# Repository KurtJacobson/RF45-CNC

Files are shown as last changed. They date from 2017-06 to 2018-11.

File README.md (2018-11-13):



# RF45-CNC
Documentation, CAD models and LinuxCNC configs for ENCO RF45 CNC conversion

Google Photos Album: https://goo.gl/photos/A5knVXhwu5FXMWHDA  
CNCzone Build Thread: http://www.cnczone.com/forums/rf-45-clone-mill/326994-cnc-cad-engineering.html  



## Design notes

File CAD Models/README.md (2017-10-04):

# CAD Models

All CAD models and drawings were made using SolidWorks 16-17.  

Currently CAD achives are available in these formats:

  * SolidWorks 16-17
  * Fusion 360
  * IGS
  * STEP

I may be able to provide other CAD formats upon request. [Open an Issue][1]
and I will see what I can do for you.

**Note** You should Download this entire folder so the part relations stay intact.

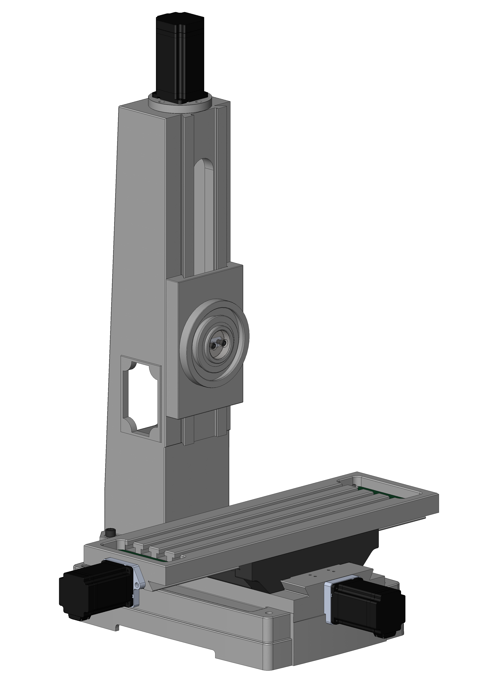
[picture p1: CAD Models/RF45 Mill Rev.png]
RF45 CAD Model Assy


[1]: https://github.com/KurtJacobson/RF45-CNC/issues/new

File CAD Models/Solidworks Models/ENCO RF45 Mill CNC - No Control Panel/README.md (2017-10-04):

# SolidWorks Models

These are SolidWorks 16-17 format solid models of the complete CNC conversion. 
I may be able to provide other CAD formats upon request, just [open an Issue][1]
and I will see what I can do for you.

**Note** You should Download this entire folder so the part relations stay intact. 

[1]: https://github.com/KurtJacobson/RF45-CNC/issues/new

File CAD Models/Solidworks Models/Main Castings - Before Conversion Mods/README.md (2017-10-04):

The CAD files in this folder are very accurate models of the original castings
before any modifications for CNC conversion. Very accurate means that critical
dimensions such as ways and hole locations are within about .005 of what they
measured on my machine, noncritical dimensions such as casting wall thicknesses
should be within about .05. You machine will likely very significantly from mine,
use with discretion.

File format is Solidworks 2016-17.  I might be able to provide other file formats 
on request.

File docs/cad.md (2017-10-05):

# CAD Models

All CAD models and drawings were made using SolidWorks 16-17. 

## CAD Archives

These are archives that I have made for various people over time. They may not
be up to date. If you can use SolidWorks files then you should download from 
the [SolidWorks Modles][2] directory.

CAD archives are available in these formats:

  * SolidWorks 16-17
  * Fusion 360
  * STEP
  * IGS

These files are located in the [`CAD Models/CAD Archives`][1] directory.

I may be able to provide other CAD formats upon request. [Open an Issue][i]
and I will see what I can do for you.

## SolidWorks Models

This is my working directory and has the most up to date models. There are two
subdirectories, one contains the models of the main castings pre-conversion, and
before any modifications. The other contains the models of the converted machine.

These files are located in the [`CAD Models/SolidWorks Models`][2] directory and
are all in SolidWorks 16-17 format.

[1]: https://github.com/KurtJacobson/RF45-CNC/tree/master/CAD%20Models/CAD%20Archives
[2]: https://github.com/KurtJacobson/RF45-CNC/tree/master/CAD%20Models/Solidworks%20Models

[i]: https://github.com/KurtJacobson/RF45-CNC/issues/new

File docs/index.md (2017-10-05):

# RF45 CNC Conversion

!!! note ""
    I will be moving all the CAD and other files from my [Google drive][1] site to here.

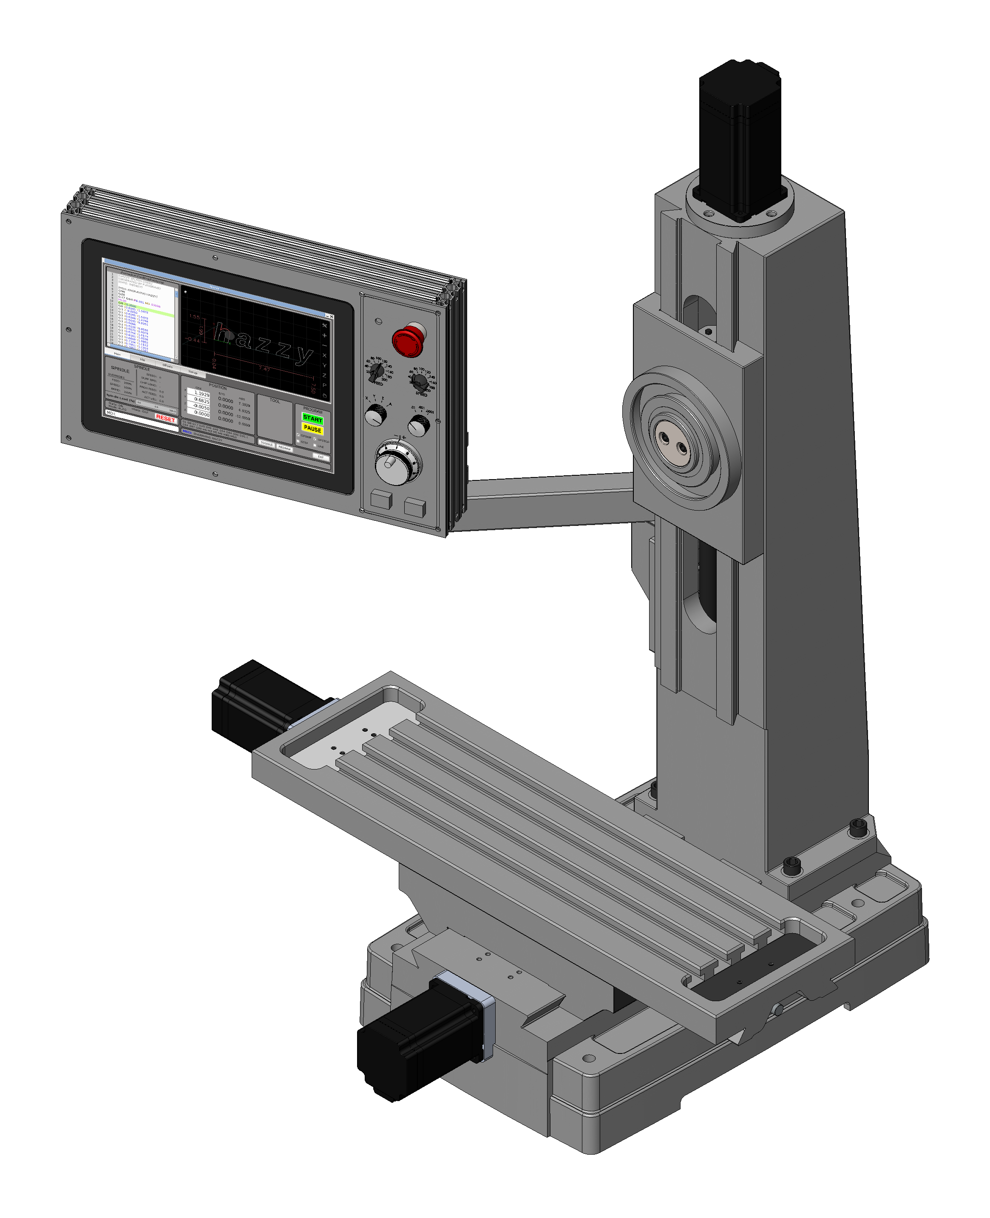
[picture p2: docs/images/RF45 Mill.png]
ENCO RF45 Clone Mill


[1]: https://drive.google.com/open?id=0B0f9qd4rM52xaklJd1I3blZVd1k

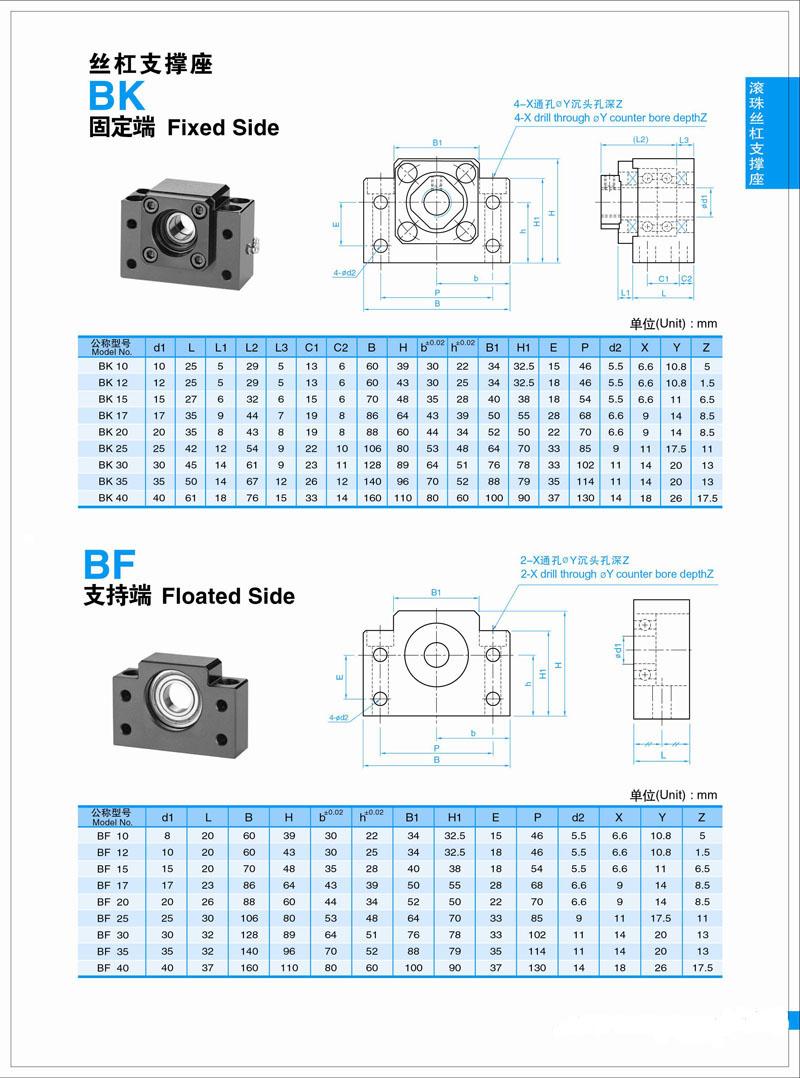
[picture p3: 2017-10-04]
CAD Models/Solidworks Models/ENCO RF45 Mill CNC - No Control Panel/X-axis/BK15/BK BF.jpg

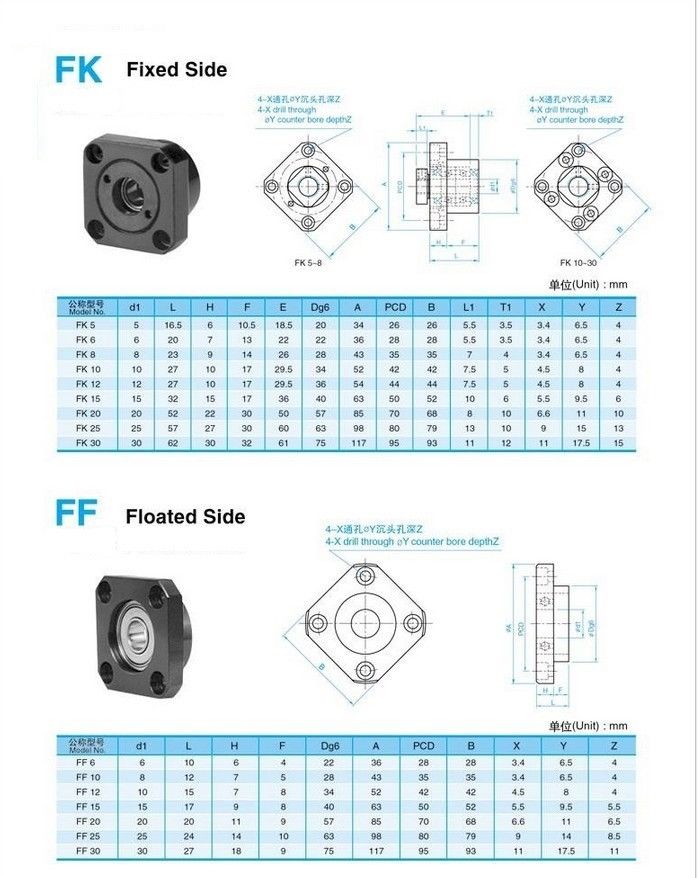
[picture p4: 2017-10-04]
CAD Models/Solidworks Models/ENCO RF45 Mill CNC - No Control Panel/Z-axis/FK15_WBK15 Flanged End Bearing/FK FF.jpg

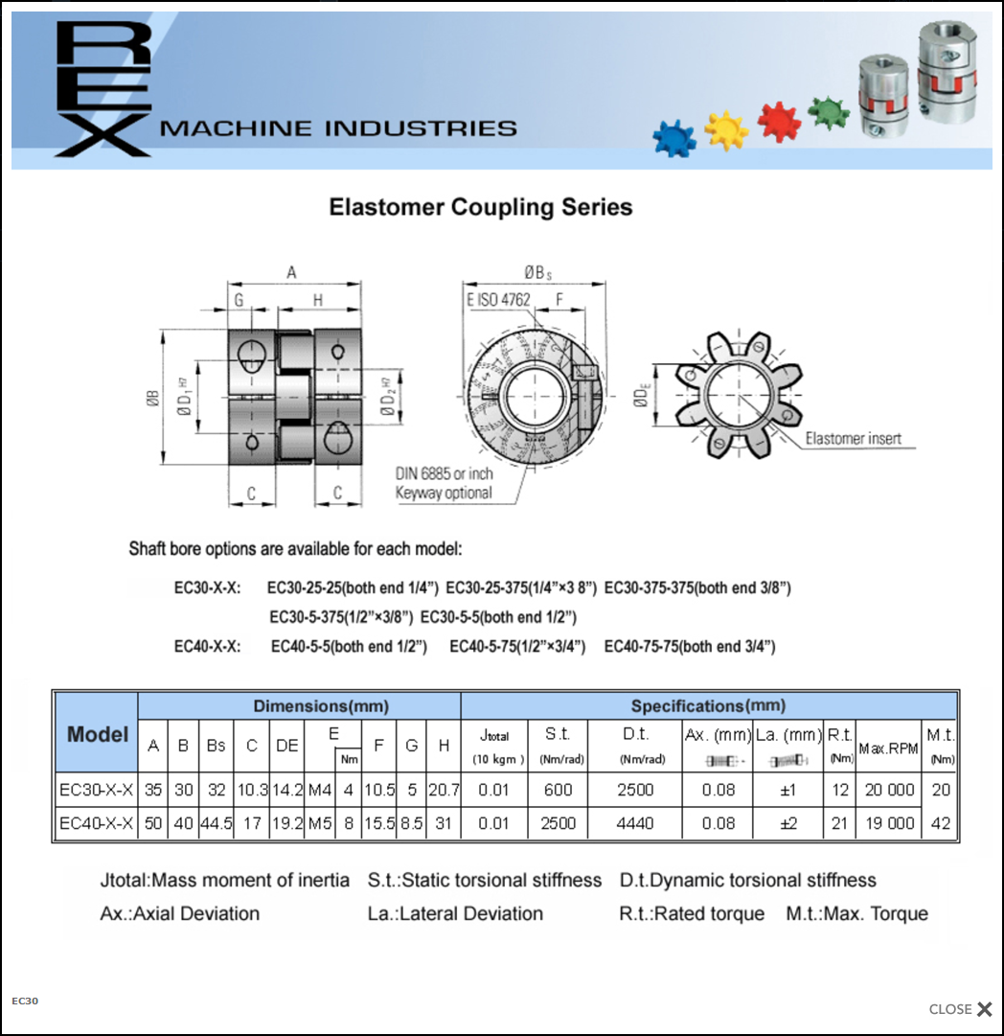
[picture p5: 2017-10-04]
CAD Models/Solidworks Models/ENCO RF45 Mill CNC - No Control Panel/Axis Drives and Couplings/GS14 Coupling/35X30 COUPLING.PNG

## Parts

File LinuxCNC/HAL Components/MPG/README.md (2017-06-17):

## MPG HAL Component

### NAME  
&nbsp;&nbsp;&nbsp;&nbsp;&nbsp;&nbsp; mpg − 4 axis MPG with multiplexed axis and increment selector switches

### SYNOPSIS
&nbsp;&nbsp;&nbsp;&nbsp;&nbsp;&nbsp; loadrt mpg[count=N|names=name1[,name2...]]

### FUNCTIONS
&nbsp;&nbsp;&nbsp;&nbsp;&nbsp;&nbsp; **mpg.**_N_

### PINS  
&nbsp;&nbsp;&nbsp;&nbsp;&nbsp;&nbsp; **mpg.**_N_**.axis0** bit in  
&nbsp;&nbsp;&nbsp;&nbsp;&nbsp;&nbsp; &nbsp;&nbsp;&nbsp;&nbsp;&nbsp;&nbsp; Input from out0 of the axis selection switch  

&nbsp;&nbsp;&nbsp;&nbsp;&nbsp;&nbsp; **mpg.**_N_**.axis1** bit in  
&nbsp;&nbsp;&nbsp;&nbsp;&nbsp;&nbsp; &nbsp;&nbsp;&nbsp;&nbsp;&nbsp;&nbsp; Input from out1 of the axis selection switch

&nbsp;&nbsp;&nbsp;&nbsp;&nbsp;&nbsp; **mpg.**_N_**.scale0** bit in  
&nbsp;&nbsp;&nbsp;&nbsp;&nbsp;&nbsp; &nbsp;&nbsp;&nbsp;&nbsp;&nbsp;&nbsp; Input from out0 of the scale selection switch

&nbsp;&nbsp;&nbsp;&nbsp;&nbsp;&nbsp; **mpg.**_N_**.scale1** bit in  
&nbsp;&nbsp;&nbsp;&nbsp;&nbsp;&nbsp; &nbsp;&nbsp;&nbsp;&nbsp;&nbsp;&nbsp; Input from out1 of the scale selection switch

&nbsp;&nbsp;&nbsp;&nbsp;&nbsp;&nbsp; **mpg.**_N_**.mpg_scale** float out  
&nbsp;&nbsp;&nbsp;&nbsp;&nbsp;&nbsp; &nbsp;&nbsp;&nbsp;&nbsp;&nbsp;&nbsp; Outputs selected mpg scale

&nbsp;&nbsp;&nbsp;&nbsp;&nbsp;&nbsp; **mpg.**_N_**.enable-x** bit out  
&nbsp;&nbsp;&nbsp;&nbsp;&nbsp;&nbsp; &nbsp;&nbsp;&nbsp;&nbsp;&nbsp;&nbsp; _TRUE_ if x-axis is selected (**axis0**=_FALSE_ and **axis1**=_FALSE_)

&nbsp;&nbsp;&nbsp;&nbsp;&nbsp;&nbsp; **mpg.**_N_**.enable-y** bit out  
&nbsp;&nbsp;&nbsp;&nbsp;&nbsp;&nbsp; &nbsp;&nbsp;&nbsp;&nbsp;&nbsp;&nbsp; _TRUE_ if y-axis is selected (**axis0**=_TRUE_ and **axis1**=_FALSE_)

&nbsp;&nbsp;&nbsp;&nbsp;&nbsp;&nbsp; **mpg.**_N_**.enable-z** bit out  
&nbsp;&nbsp;&nbsp;&nbsp;&nbsp;&nbsp; &nbsp;&nbsp;&nbsp;&nbsp;&nbsp;&nbsp; _TRUE_ if z-axis is selected (**axis0**=_FALSE_ and **axis1**=_TRUE_)

&nbsp;&nbsp;&nbsp;&nbsp;&nbsp;&nbsp; **mpg.**_N_**.enable-a** bit out  
&nbsp;&nbsp;&nbsp;&nbsp;&nbsp;&nbsp; &nbsp;&nbsp;&nbsp;&nbsp;&nbsp;&nbsp; _TRUE_ if a-axis is selected (**axis0**=_TRUE_ and **axis1**=_TRUE_)

### PARAMETERS  

&nbsp;&nbsp;&nbsp;&nbsp;&nbsp;&nbsp; **mpg.**_N_**.mpg-scale1** float rw (default: _.01_)  
&nbsp;&nbsp;&nbsp;&nbsp;&nbsp;&nbsp; &nbsp;&nbsp;&nbsp;&nbsp;&nbsp;&nbsp; Desired jog scale for first increment switch position  

&nbsp;&nbsp;&nbsp;&nbsp;&nbsp;&nbsp; **mpg.**_N_**.mpg-scale2** float rw (default: _.001_)  
&nbsp;&nbsp;&nbsp;&nbsp;&nbsp;&nbsp; &nbsp;&nbsp;&nbsp;&nbsp;&nbsp;&nbsp; Desired jog scale for second increment switch position  

&nbsp;&nbsp;&nbsp;&nbsp;&nbsp;&nbsp; **mpg.**_N_**.mpg-scale3** float rw (default: _.0001_)  
&nbsp;&nbsp;&nbsp;&nbsp;&nbsp;&nbsp; &nbsp;&nbsp;&nbsp;&nbsp;&nbsp;&nbsp; Desired jog scale for third increment switch position  

&nbsp;&nbsp;&nbsp;&nbsp;&nbsp;&nbsp; **mpg.**_N_**.mpg-scale4** float rw (default: _.00001_)  
&nbsp;&nbsp;&nbsp;&nbsp;&nbsp;&nbsp; &nbsp;&nbsp;&nbsp;&nbsp;&nbsp;&nbsp; Desired jog scale for fourth increment switch position  

&nbsp;&nbsp;&nbsp;&nbsp;&nbsp;&nbsp; **mpg.**_N_**.mpg_pulses** s32 rw (default: 4)  
&nbsp;&nbsp;&nbsp;&nbsp;&nbsp;&nbsp; &nbsp;&nbsp;&nbsp;&nbsp;&nbsp;&nbsp; Number of pulses per MPG detent  

### LICENSE

&nbsp;&nbsp;&nbsp;&nbsp;&nbsp;&nbsp; GPL

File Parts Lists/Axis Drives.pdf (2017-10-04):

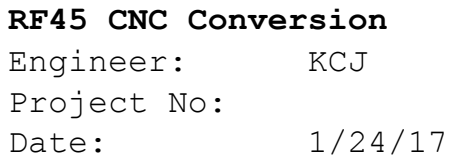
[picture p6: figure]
RF45 CNC Conversion; Engineer:; KCJ; Project No:; Date:

1-1

### Parts List for RF45 CNC Conversion Hybrid Servo Axis Drives

Parts List

P/N | NAME: | Date: 1/24/17
Designed BY: | DRAWINGS: | PAGE: 1 OF 1
TAG No. | DESCRIPTION | Manufacture | Part No. | QTY. | Unit Cost | Total Cost
1 | NEMA 34 1200 oz-in Stepper Motor w/ 1000 line encoder For X & Y | SuTai | 86HSS1402 | 2 | $38.34 | $76.68
2 | NEMA 34 1600 oz-in Stepper Motor w/ 1000 line encoder For Z | SuTai | 86HSS5001 | 1 | $51.60 | $51.60
3 | 8.2A Closed loop stepper driver | SuTai | HBS86H | 3 | $55.56 | $166.68
4 | Shipping via DHL | | | | | $140.30
| | | | | Total: | $435.26

NOTES:
I purchased the motors and drives directly from Changzhou Sutai Electrical Co.,Ltd in China towards the end of July 16. Jinting Wen is the fellow to talk to about ordering. He is very knowledgeable and answered all my questions, in English!

Mike Hall on CNCzone found what looks to be the same motors listed on Alibaba: https://sutai.en.alibaba.com/product/60553941360-801999927/6A_12Nm_1_8_degree_nema_34_china_closed_loop_cnc_stepper_motor_kit.html (https://sutai.en.alibaba.com/product/60553941360-801999927/6A_12Nm_1_8_degree_nema_34_china_closed_loop_cnc_stepper_motor_kit.html)

Thanks for the link, Mike!

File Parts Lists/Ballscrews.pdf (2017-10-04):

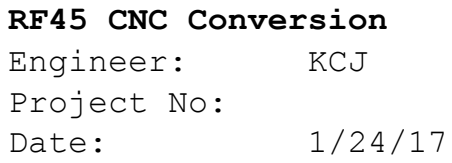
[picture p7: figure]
RF45 CNC Conversion; Engineer:; KCJ; Project No:; Date:

1-1

### Parts List for RF45 CNC Conversion X, Y & Z Ballscrews

Parts List

P/N | NAME: | Date: 1/24/17
Designed BY: KCJ | DRAWINGS: See Google Drive Folder | PAGE: 1 OF 1
TAG No. | DESCRIPTION | Manufacture | Part No. | QTY. | Unit Cost | Total Cost
1 | X-axis Ballscrew RM2005 x 772mm | Chai | N/A | 1 | N/A
2 | Y-axis Ballscrew RM2005 x 677mm | Chai | N/A | 1 | N/A
3 | Z-axis Ballscrew RM2005 x 602mm | Chai | N/A | 1 | N/A
4 | RM2005 Ballnut | Chai | N/A | 6 | N/A
5 | BK15 Block type fixed end support for X & Y | Chai | N/A | 2 | N/A
6 | BF15 Block type free end support for X | Chai | N/A | 1 | N/A
7 | FK15 Flange type fixed end support for Z | Chai | N/A | 1 | N/A
| | | | | Total: | $216.50

NOTES:
Chai is the fellow that runs the ebay store linearmotionbearings2008 (http://www.ebay.com/usr/linearmotionbearings2008) It seems best just to email him with your order.
Air shipping was included in the cost and was very fast.

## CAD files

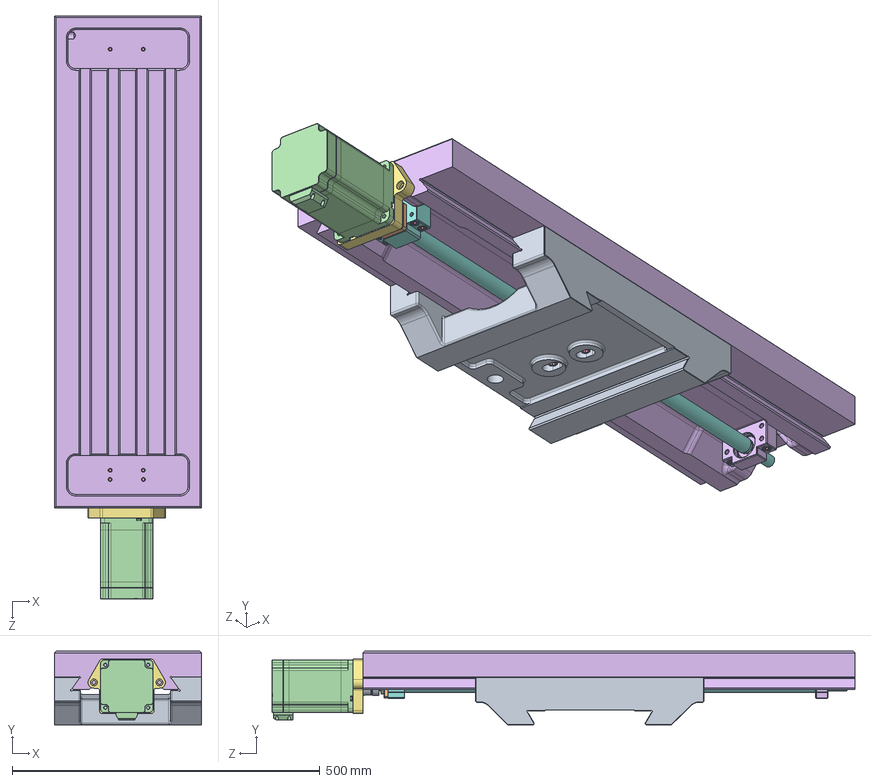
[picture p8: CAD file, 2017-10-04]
CAD Models/Solidworks Models/ENCO RF45 Mill CNC - No Control Panel/X-axis/X-axis Assy.SLDASM
239.7 x 119.6 x 948.0 mm
Saddle
X-axis Ballnut Mount
2005 ballnut x 2
0.25-20 BHCS x 12
0.313-18 SHCS x 2
Mill Table
X-axis Motor Mount
BK15 Block - Modified
BK15 Spacer x 2
BK15 Flange
7002 AC Bearing x 2
BK15 Nut
SET SCREW x 2
BK15 Seal x 2
SHCS x 4
X-axis RM2005-C7
GS14-HUB x 2
GS14-SPIDER
M4 SHCS x 2
NEMA 34 Stepper Motor
0.25-20 SHCS x 6
BF15 Free End Bearing

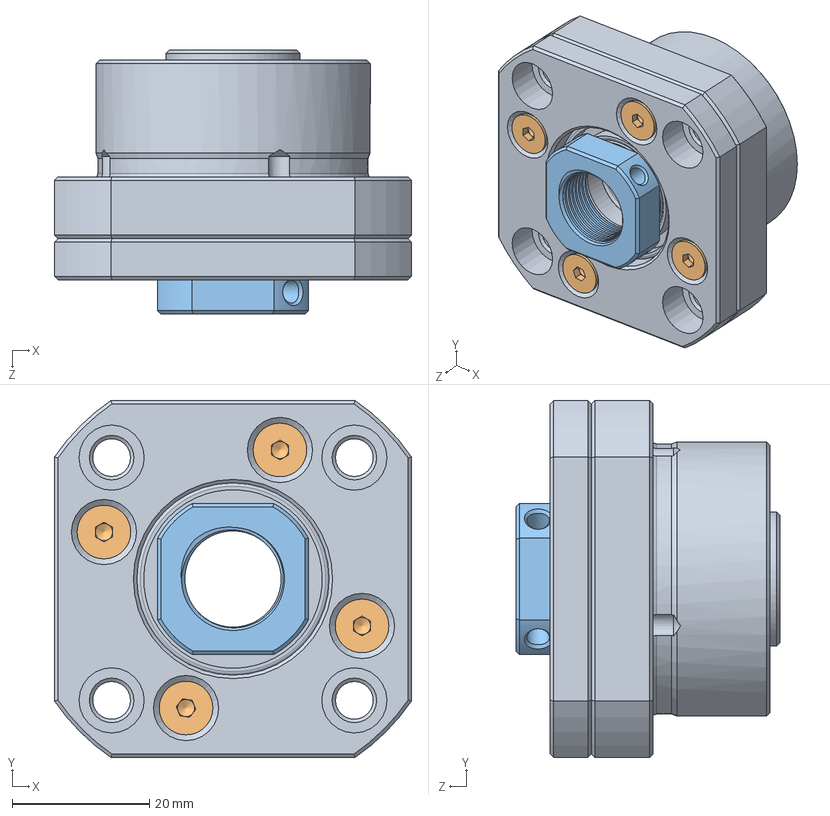
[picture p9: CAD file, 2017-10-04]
CAD Models/Solidworks Models/ENCO RF45 Mill CNC - No Control Panel/Z-axis/FK15_WBK15 Flanged End Bearing/WBK_15 End Bearing.SLDASM
52.0 x 52.0 x 38.5 mm
FK15_WBK-15
M4 x 12 SHFS x 4
Lock Nut

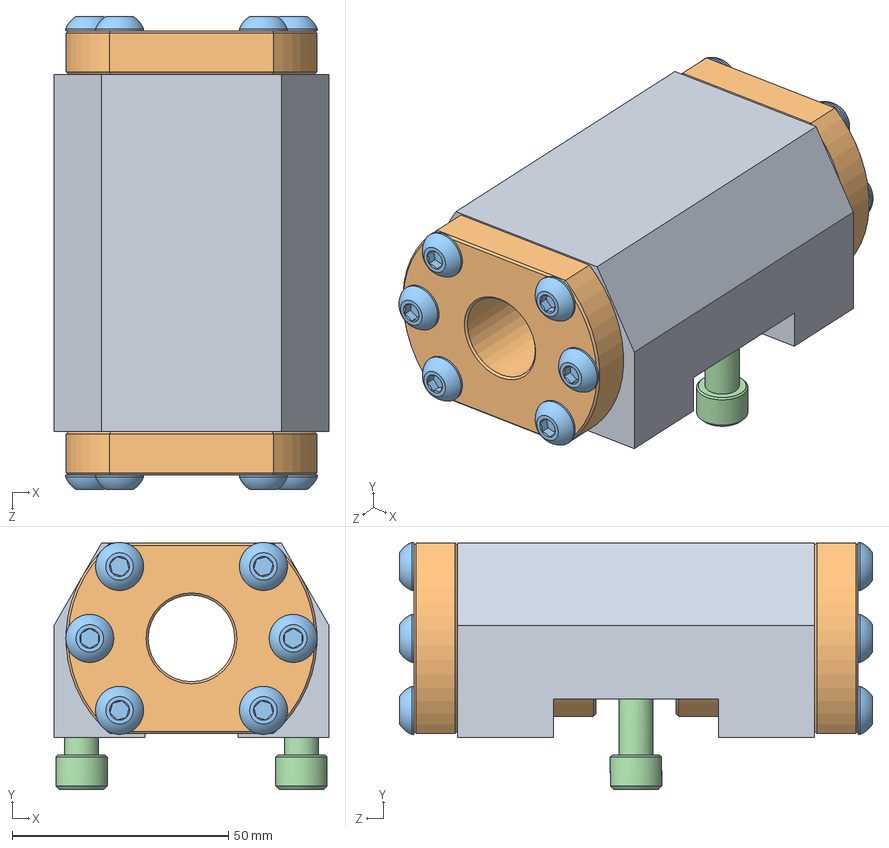
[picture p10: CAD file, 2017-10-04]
CAD Models/Solidworks Models/ENCO RF45 Mill CNC - No Control Panel/X-axis/X-axis Ballnut Mount.SLDASM
63.5 x 57.1 x 109.3 mm
X-axis Ballnut Mount
2005 ballnut x 2
0.25-20 BHCS x 12
0.313-18 SHCS x 2

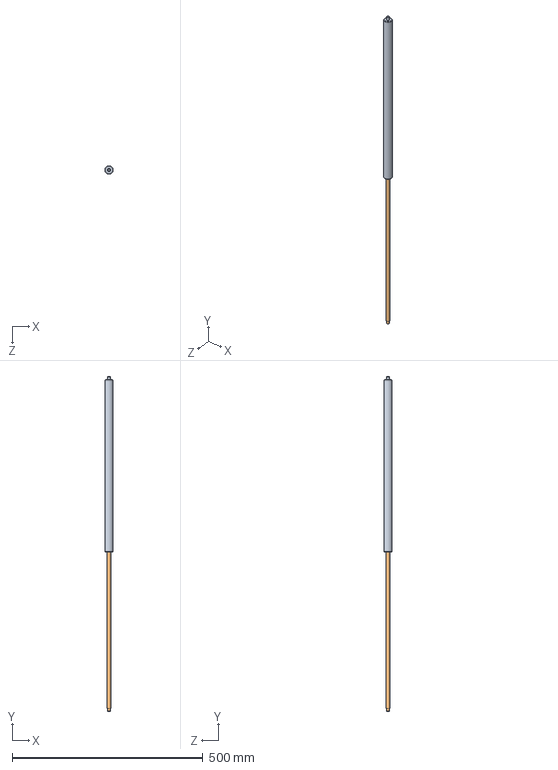
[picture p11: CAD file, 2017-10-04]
CAD Models/Solidworks Models/ENCO RF45 Mill CNC - No Control Panel/Z-axis/100 lb Strut Assy/Strut Assy.SLDASM
22.1 x 878.8 x 22.1 mm
Strut Cylinder
Strut Rod

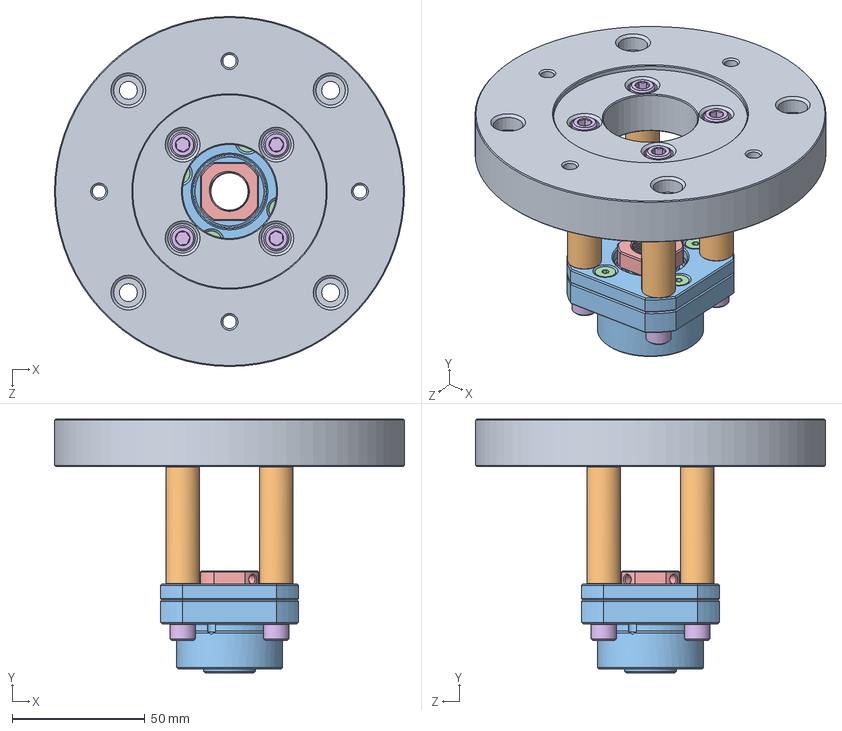
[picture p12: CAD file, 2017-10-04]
CAD Models/Solidworks Models/ENCO RF45 Mill CNC - No Control Panel/Z-axis/Z-Axis Motor Mount Assy.SLDASM
132.1 x 95.7 x 132.1 mm
Z-Axis Motor Mount
Z-axis End Bearing Standoff x 4
FK15_WBK-15
M4 x 12 SHFS x 4
Lock Nut
0.25-20 SHCS x 8

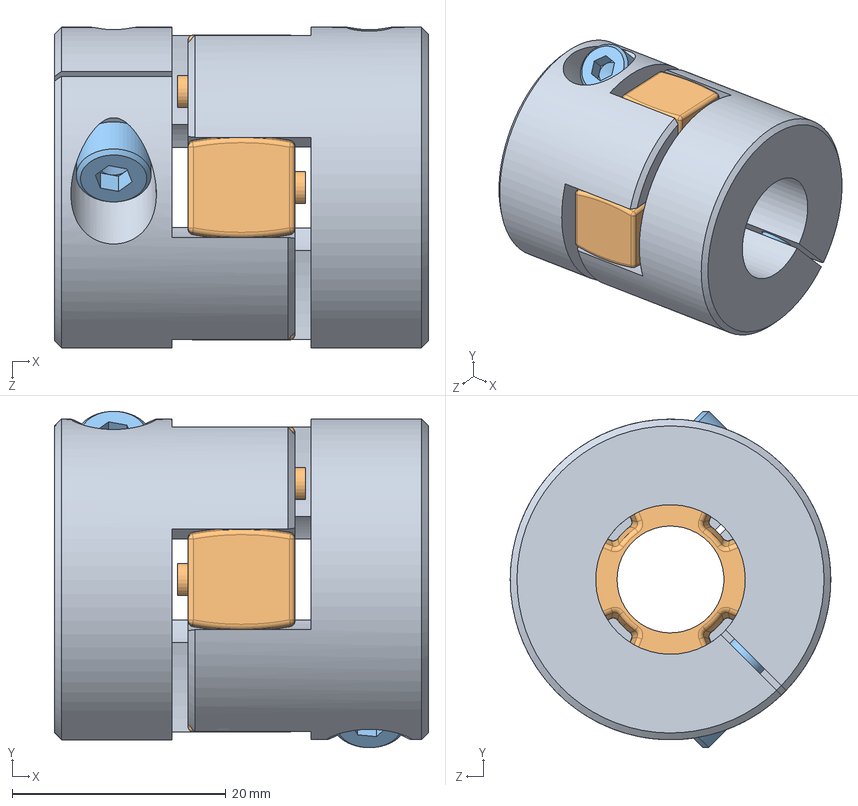
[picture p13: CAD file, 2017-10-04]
CAD Models/Solidworks Models/ENCO RF45 Mill CNC - No Control Panel/Axis Drives and Couplings/GS14 Coupling/GS14 Coupling Assy.SLDASM
35.0 x 31.5 x 30.0 mm
GS14-HUB x 2
GS14-SPIDER
M4 SHCS x 2

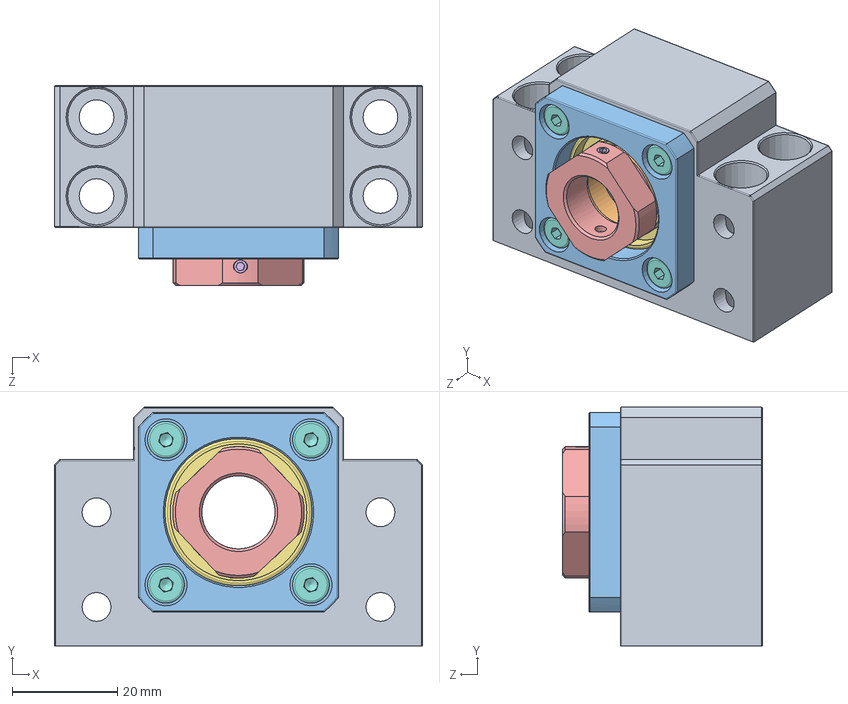
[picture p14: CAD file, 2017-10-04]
CAD Models/Solidworks Models/ENCO RF45 Mill CNC - No Control Panel/X-axis/BK15/BK15-Modified.SLDASM
70.0 x 45.4 x 38.0 mm
BK15 Block - Modified
BK15 Spacer x 2
BK15 Flange
7002 AC Bearing x 2
BK15 Nut
SET SCREW x 2
BK15 Seal x 2
SHCS x 4

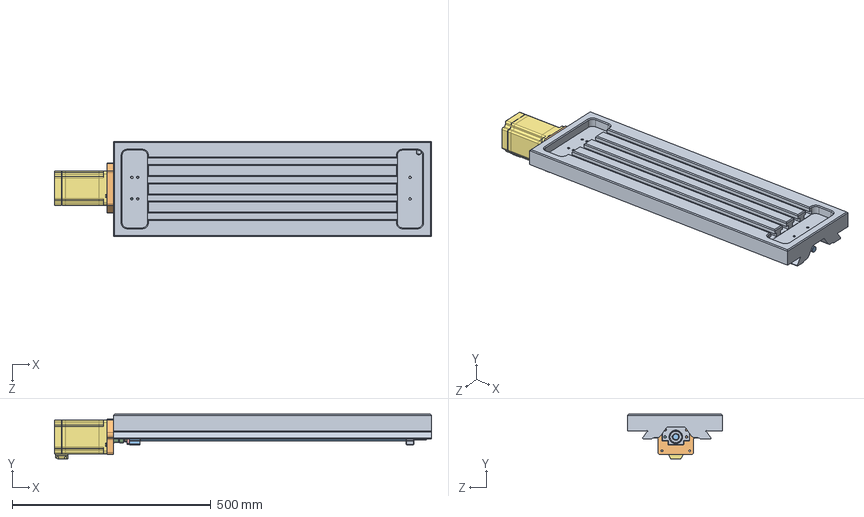
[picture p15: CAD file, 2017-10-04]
CAD Models/Solidworks Models/ENCO RF45 Mill CNC - No Control Panel/X-axis/Mill Table.SLDASM
948.0 x 111.9 x 239.7 mm
Mill Table
X-axis Motor Mount
BK15 Block - Modified
BK15 Spacer x 2
BK15 Flange
7002 AC Bearing x 2
BK15 Nut
SET SCREW x 2
BK15 Seal x 2
SHCS x 4
X-axis RM2005-C7
GS14-HUB x 2
GS14-SPIDER
M4 SHCS x 2
NEMA 34 Stepper Motor
0.25-20 SHCS
BF15 Free End Bearing

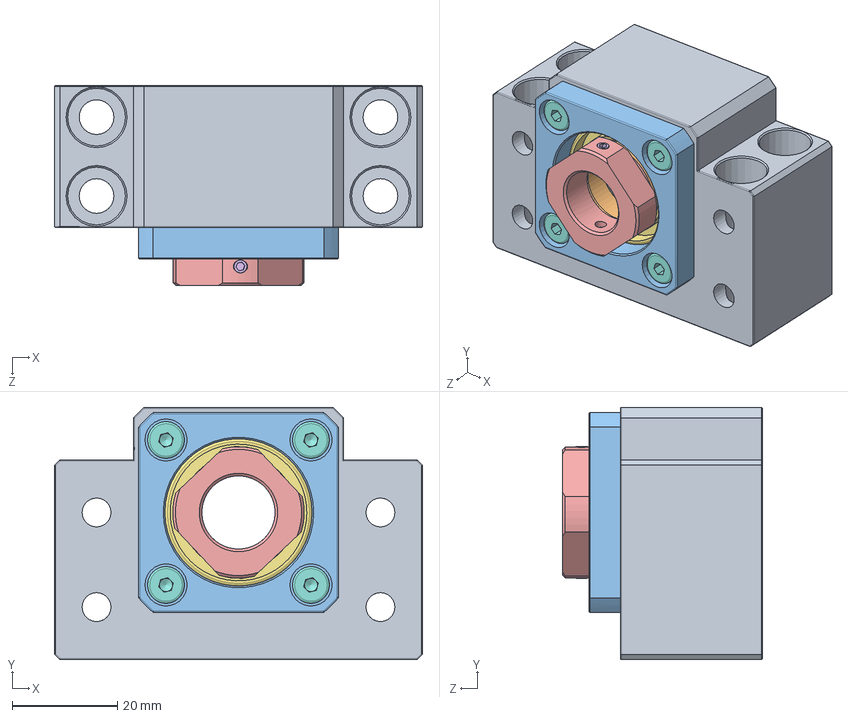
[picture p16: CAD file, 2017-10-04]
CAD Models/Solidworks Models/ENCO RF45 Mill CNC - No Control Panel/Y-axis/Y axis BK15 End Bearing/BK15.SLDASM
70.0 x 48.0 x 38.0 mm
BK15 Block
BK15 Spacer x 2
BK15 Flange
7002 AC Bearing x 2
BK15 Nut
SET SCREW x 2
BK15 Seal x 2
SHCS x 4

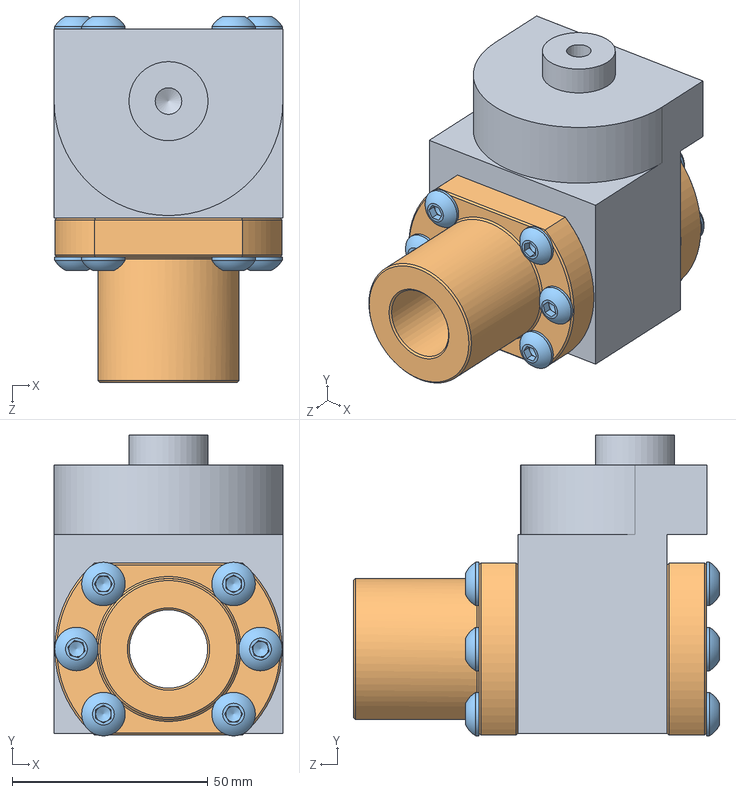
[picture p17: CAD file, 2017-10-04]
CAD Models/Solidworks Models/ENCO RF45 Mill CNC - No Control Panel/Y-axis/Y-axis Ballnut Assy.SLDASM
58.4 x 76.8 x 93.5 mm
Y-axis Ballnut Mount
2005 ballnut x 2
0.25-20 x .625 SHCS x 12

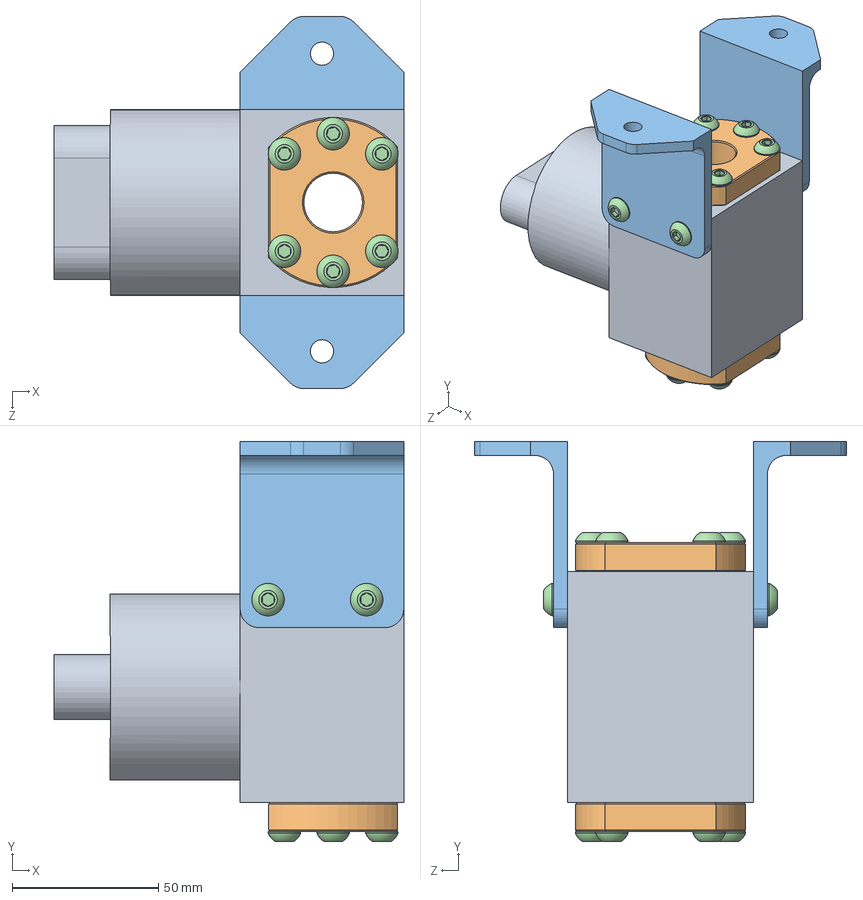
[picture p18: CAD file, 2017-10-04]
CAD Models/Solidworks Models/ENCO RF45 Mill CNC - No Control Panel/Z-axis/Z-axis Mount Assy.SLDASM
119.4 x 136.5 x 127.0 mm
Z-axis Ballnut Mount
2005 ballnut x 2
Z-axis Gas Strut Braket x 2
0.25-20 BHCS x 16

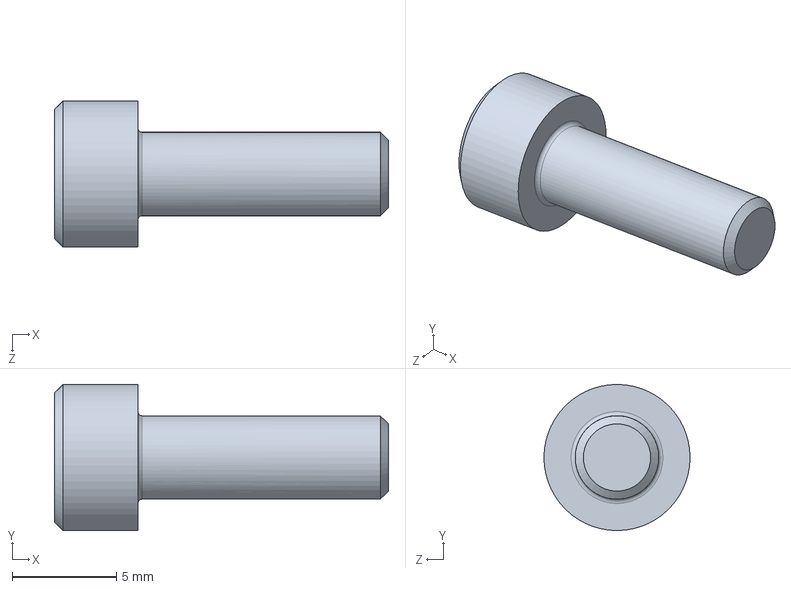
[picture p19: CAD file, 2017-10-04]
CAD Models/Solidworks Models/ENCO RF45 Mill CNC - No Control Panel/Axis Drives and Couplings/GS14 Coupling/M4 SHCS.SLDPRT
16.0 x 7.00 x 7.00 mm

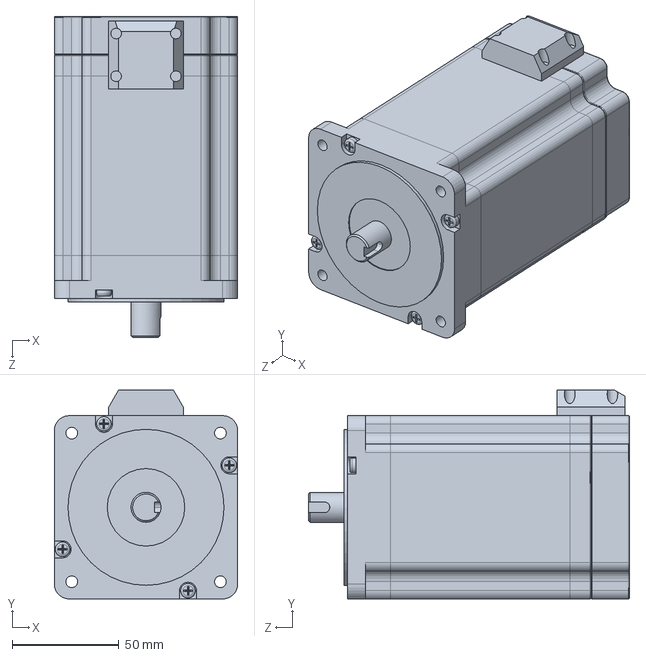
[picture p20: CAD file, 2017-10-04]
CAD Models/Solidworks Models/ENCO RF45 Mill CNC - No Control Panel/Axis Drives and Couplings/NEMA 34 Stepper Motor.SLDPRT
85.8 x 97.8 x 150.3 mm

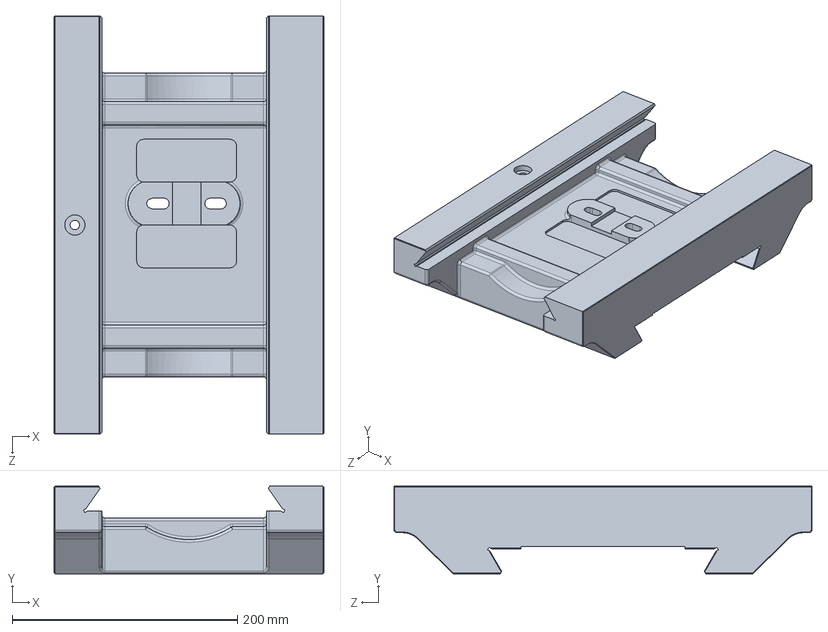
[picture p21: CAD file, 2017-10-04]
CAD Models/Solidworks Models/ENCO RF45 Mill CNC - No Control Panel/Main Castings/Saddle.SLDPRT
239.7 x 77.8 x 371.5 mm

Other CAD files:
CAD Models/Solidworks Models/ENCO RF45 Mill CNC - No Control Panel/X-axis/BF15/BF15 Free End Bearing.SLDPRT
CAD Models/Solidworks Models/ENCO RF45 Mill CNC - No Control Panel/Y-axis/Y axis BK15 End Bearing/SHCS.SLDPRT
CAD Models/Solidworks Models/ENCO RF45 Mill CNC - No Control Panel/Z-axis/100 lb Strut Assy/Strut Cylinder.SLDPRT
CAD Models/Solidworks Models/ENCO RF45 Mill CNC - No Control Panel/Z-axis/Z-axis RM2005-C7.SLDPRT
CAD Models/CAD Archives/17-0130 RF45 - Fusion 360.f3d
CAD Models/Solidworks Models/ENCO RF45 Mill CNC - No Control Panel/Axis Drives and Couplings/2005 ballnut.SLDPRT
CAD Models/Solidworks Models/ENCO RF45 Mill CNC - No Control Panel/Axis Drives and Couplings/9712K610 Belleville Spring.SLDPRT
CAD Models/Solidworks Models/ENCO RF45 Mill CNC - No Control Panel/Axis Drives and Couplings/GS14 Coupling/GS14-HUB.sldprt
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

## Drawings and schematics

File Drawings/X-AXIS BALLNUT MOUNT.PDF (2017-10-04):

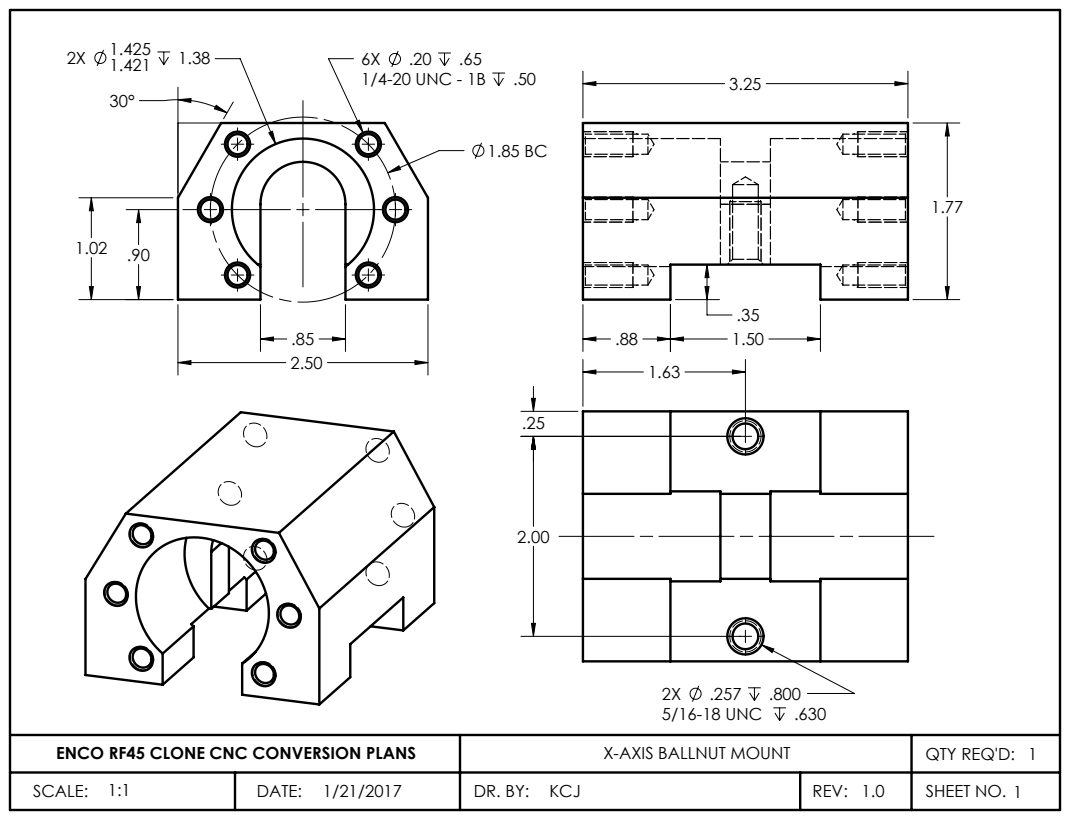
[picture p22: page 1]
1/4-20 UNC - 1B; 5/16-18 UNC

ENCO RF45 CLONE CNC CONVERSION PLANS | X-AXIS BALLNUT MOUNT | QTY REQ'D: 1
SCALE: 1:1 | DATE: 1/21/2017 | DR. BY: KCJ | REV: 1.0 | SHEET NO. 1

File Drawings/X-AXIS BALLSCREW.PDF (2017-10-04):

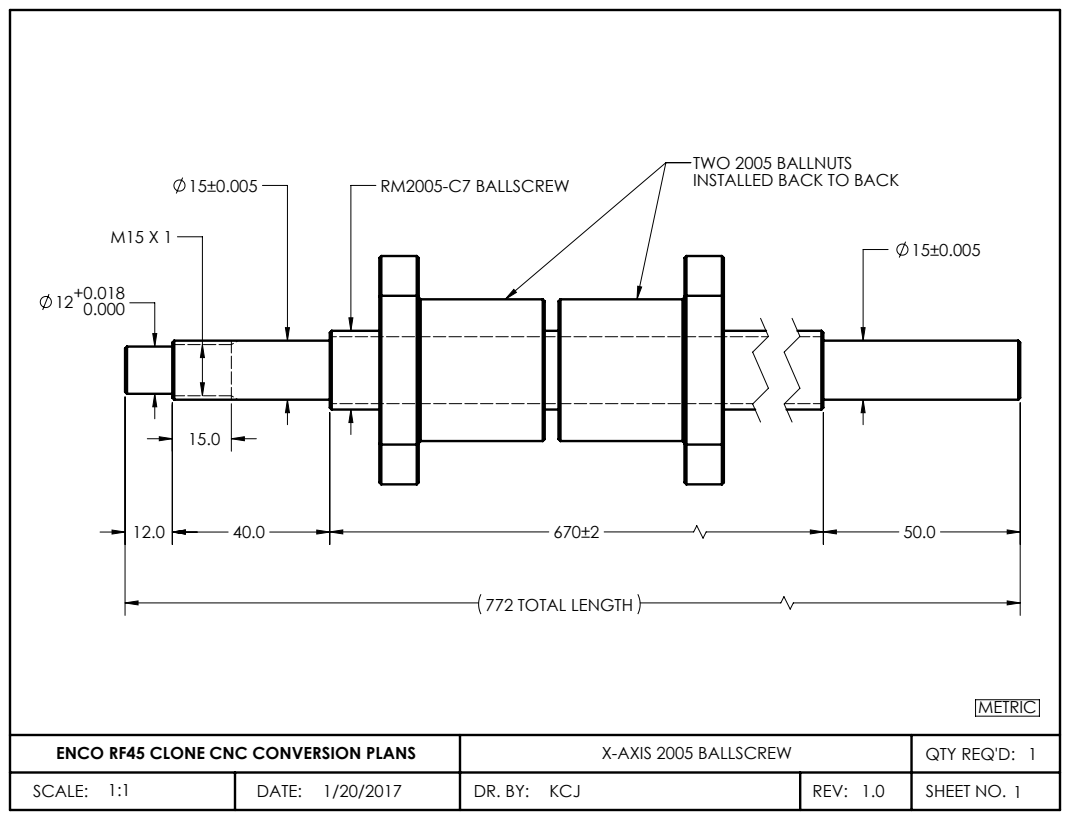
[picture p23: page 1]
RM2005-C7 BALLSCREW; 772 TOTAL LENGTH; METRIC

TWO 2005 BALLNUTS
INSTALLED BACK TO BACK

ENCO RF45 CLONE CNC CONVERSION PLANS | X-AXIS 2005 BALLSCREW | QTY REQ'D: 1
SCALE: 1:1 | DATE: 1/20/2017 | DR. BY: KCJ | REV: 1.0 | SHEET NO. 1

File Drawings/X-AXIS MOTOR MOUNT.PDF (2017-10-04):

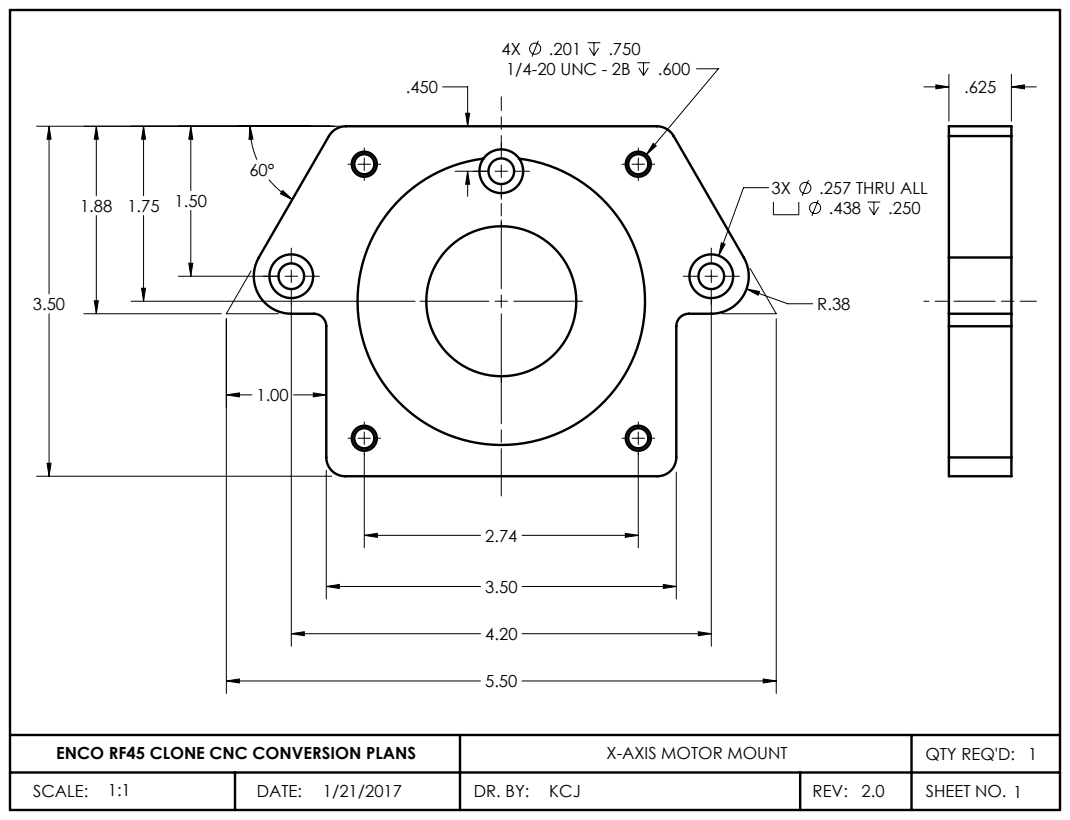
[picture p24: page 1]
1/4-20 UNC - 2B; .257 THRU ALL

ENCO RF45 CLONE CNC CONVERSION PLANS | X-AXIS MOTOR MOUNT | QTY REQ'D: 1
SCALE: 1:1 | DATE: 1/21/2017 | DR. BY: KCJ | REV: 2.0 | SHEET NO. 1

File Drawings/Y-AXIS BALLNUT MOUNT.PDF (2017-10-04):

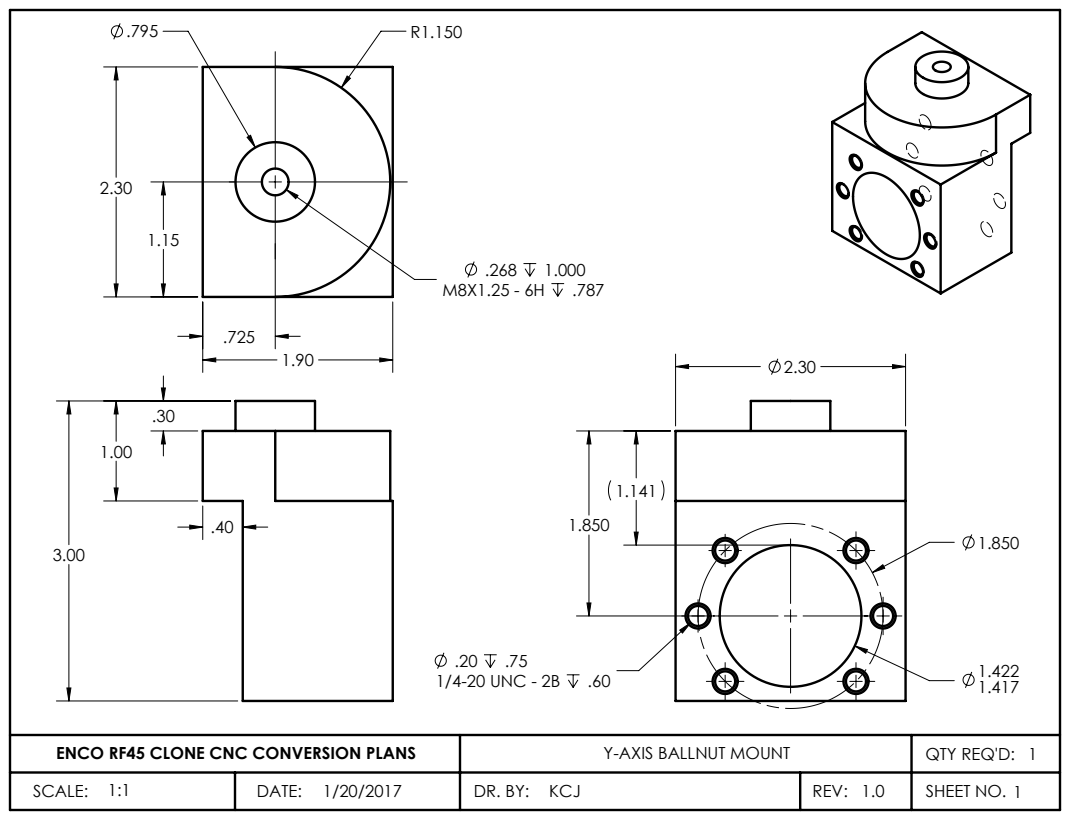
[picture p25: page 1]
1/4-20 UNC - 2B

ENCO RF45 CLONE CNC CONVERSION PLANS | Y-AXIS BALLNUT MOUNT | QTY REQ'D: 1
SCALE: 1:1 | DATE: 1/20/2017 | DR. BY: KCJ | REV: 1.0 | SHEET NO. 1

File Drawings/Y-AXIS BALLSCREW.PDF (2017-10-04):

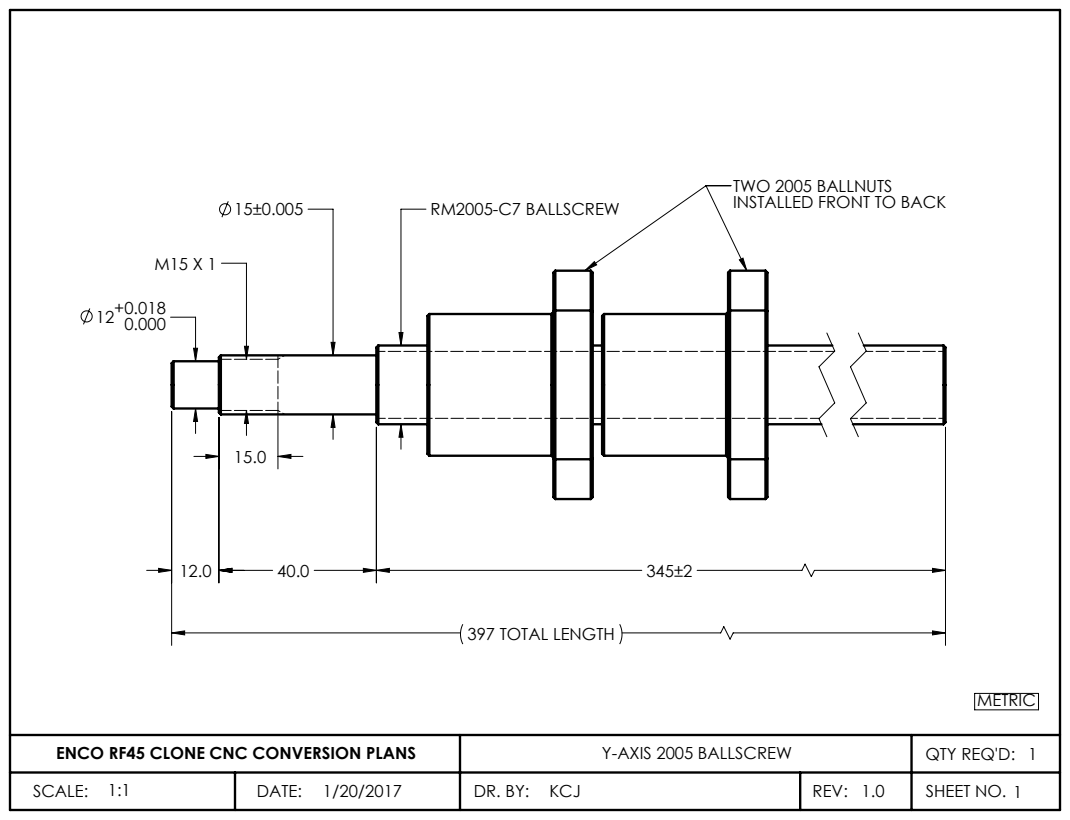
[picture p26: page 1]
RM2005-C7 BALLSCREW; 397 TOTAL LENGTH; METRIC

TWO 2005 BALLNUTS
INSTALLED FRONT TO BACK

ENCO RF45 CLONE CNC CONVERSION PLANS | Y-AXIS 2005 BALLSCREW | QTY REQ'D: 1
SCALE: 1:1 | DATE: 1/20/2017 | DR. BY: KCJ | REV: 1.0 | SHEET NO. 1

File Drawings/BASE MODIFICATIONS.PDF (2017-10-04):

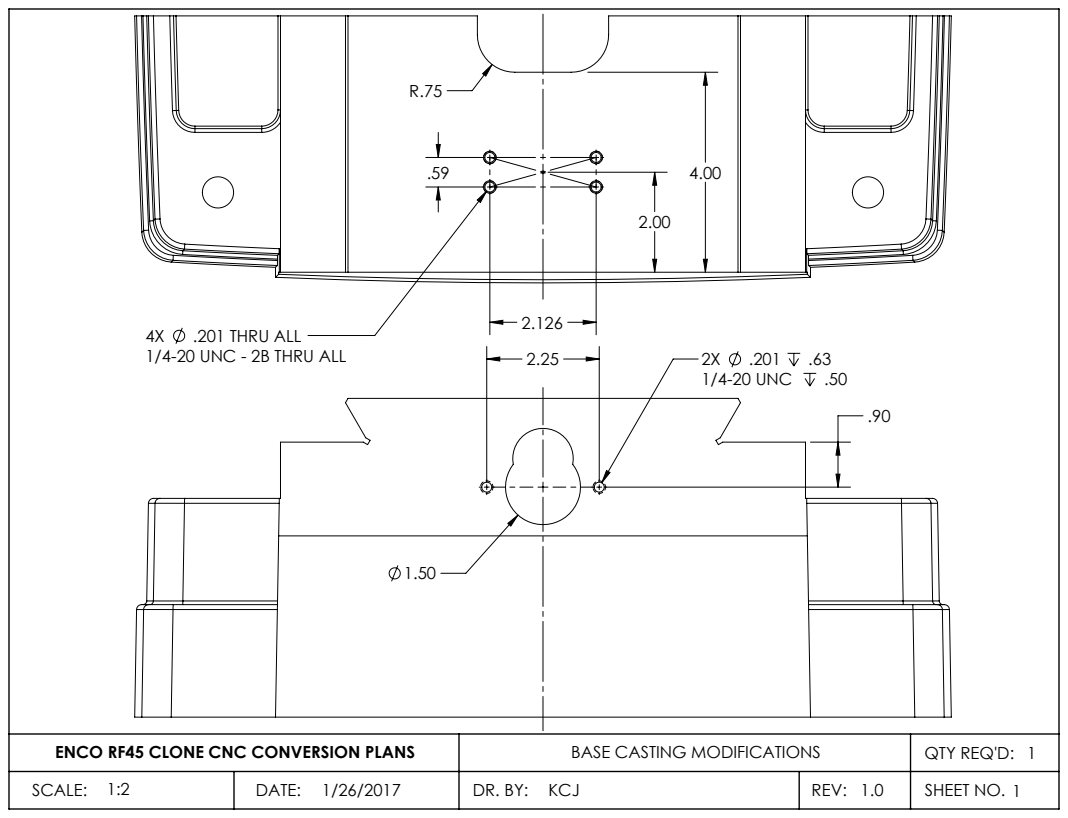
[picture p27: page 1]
1/4-20 UNC; .201 THRU ALL

1/4-20 UNC - 2B THRU ALL

ENCO RF45 CLONE CNC CONVERSION PLANS | BASE CASTING MODIFICATIONS | QTY REQ'D: 1
SCALE: 1:2 | DATE: 1/26/2017 | DR. BY: KCJ | REV: 1.0 | SHEET NO. 1

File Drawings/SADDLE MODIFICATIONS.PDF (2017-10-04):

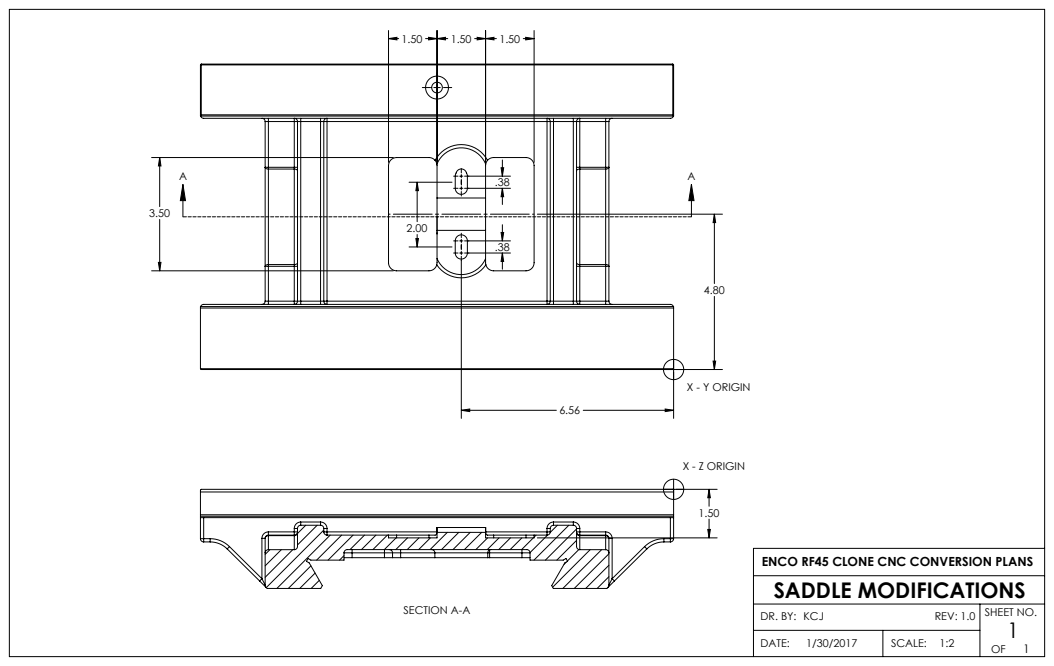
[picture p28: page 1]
X - Y ORIGIN; SECTION A-A; X - Z ORIGIN

ENCO RF45 CLONE CNC CONVERSION PLANS
SADDLE MODIFICATIONS

DR. BY: KCJ REV: 1.0 | SHEET NO. 1 OF 1

1/30/2017 DATE: | 1:2 SCALE:

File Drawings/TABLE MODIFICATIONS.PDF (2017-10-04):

A

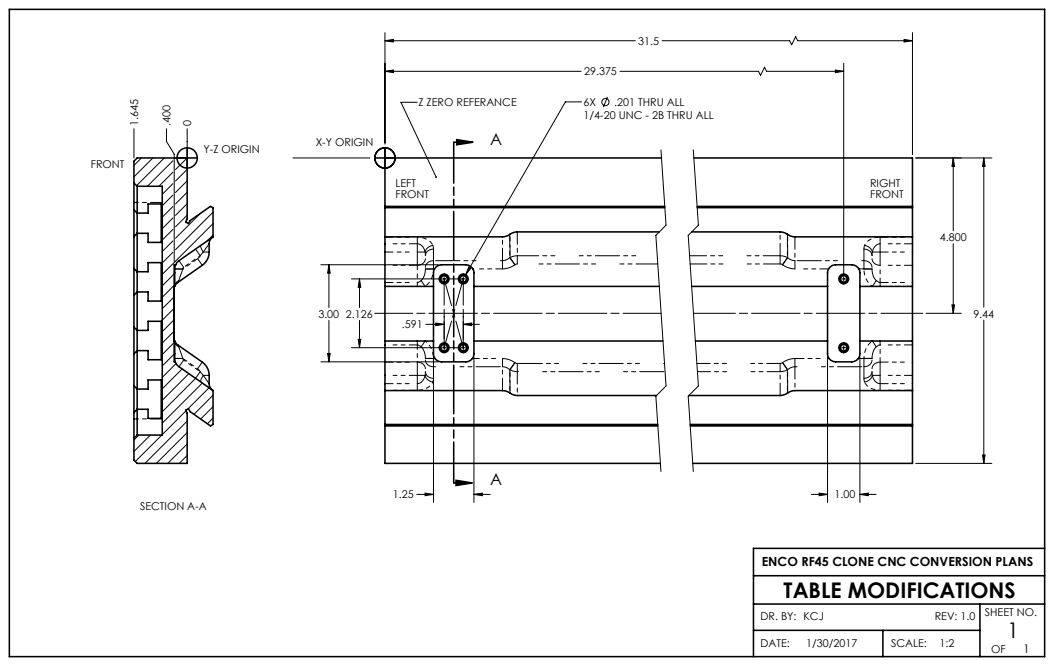
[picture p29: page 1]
.201 THRU ALL; LEFT FRONT; X-Y ORIGIN; Z ZERO REFERANCE; SECTION A-A; RIGHT FRONT; FRONT; Y-Z ORIGIN

1/4-20 UNC - 2B THRU ALL

ENCO RF45 CLONE CNC CONVERSION PLANS
TABLE MODIFICATIONS

DR. BY: KCJ REV: 1.0 | SHEET NO. 1 OF 1

1/30/2017 DATE: | 1:2 SCALE:

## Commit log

2017-10-04 Add CAD Models
    [0.25-20 BHCS.SLDPRT, 0.25-20 SHCS.SLDPRT, 0.25-20 x .625 SHCS.SLDPRT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]
2017-10-04 Embed CAD image
2017-10-05 Add cad.md
2017-11-03 Add link to CNCzone thread
